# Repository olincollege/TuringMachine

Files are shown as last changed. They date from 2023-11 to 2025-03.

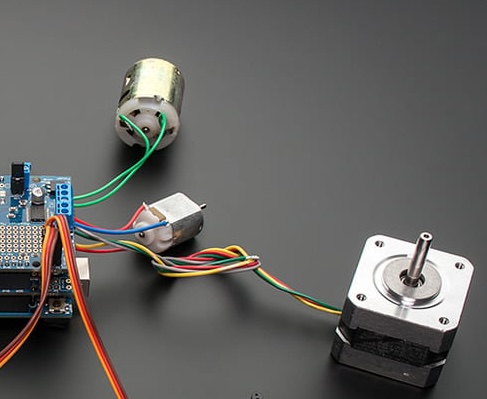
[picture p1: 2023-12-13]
website/turing-machine/images/actuation_motors.jpg

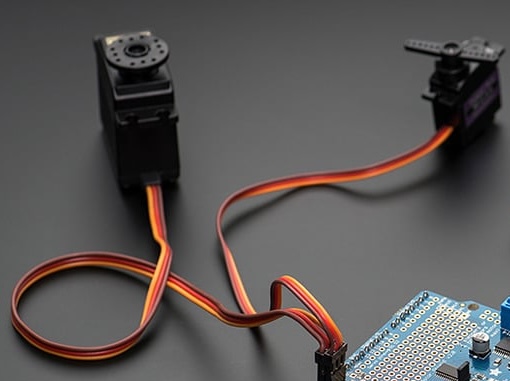
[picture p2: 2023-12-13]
website/turing-machine/images/servos.jpg

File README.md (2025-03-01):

# Turing Machine

**Developed by:** Sparsh Gupta, Mark Belanger, Noah Rand, Joe Leedy, Will Young

Developed at Olin College of Engineering for the Principles of Integrated Engineering (Fall 2023) final project.

[STORY: Olin Students Create Rare, Fully Functional Electromechanical Turing Machine](https://www.olin.edu/articles/story-olin-students-create-rare-fully-functional-electromechanical-turing-machine)

### About
This project is a physical electromechanical implementation of a [Universal Turing Machine](https://en.wikipedia.org/wiki/Universal_Turing_machine) that currently supports basic Turing-computational operations and a few Turing-complete languages.

It could be modified easily to support more Turing-computable operations and Turing-complete languages.

Learn more at: https://olincollege.github.io/pie-2023-03/turing-machine/

### Operations
List of operations currently supported:

- **anbn** (check whether a string has an equal number of 0s and 1s)
- **palindrome** (check whether a string of 0s and 1s is a palindrome)
- **booleanNot** (check whether a string is the boolean NOT/complement of another string)
- **booleanOr** (check whether a string is the boolean OR output of two other strings)
- **addition** (check whether a string is the binary addition output of two other strings)

### Strings/Language

Sample string input formats or languages accepted by the Turing Machine for operations:

**anbn**: 00, 1010, 0110, etc. (any string of even length that consists of 0s and 1s)

**palindrome**: 010, 1001, 111, etc. (any string that consists of 0s and 1s)

**booleanNot**: #0#1, #110#001, #10#01, etc. (two strings u and v that consist of 0s and 1s in the form #u#v 
such that (NOT u = v))

**booleanOr**: #0#1#1, "#101#010#111", etc. (three strings u, v, and w that consist of 0s and 1s in the form #u#v#w 
such that (u OR v = w))

**addition**: #0#1#1, #01#01#10, #101#010#111, etc. (three strings u, v, and w that consist of 0s and 1s in the form #u#v#w 
such that (u + v = w))

### Brief structure of repo

The `CAD` directory houses all the design, fabrication, and mechanical aspects of the project.

The `code` directory contains the entire codebase for simulating the Turing Machine. The subdirectory `main` contains the code flashed to Arduino UNO for motor functions,
state transition, and state transition operations. The subdirectory `symbol_recognition` contains the code for classifying the bits written on tape and is flashed to the ESP32-Cam.

The `website` directory contains the entire code for our hosted website.

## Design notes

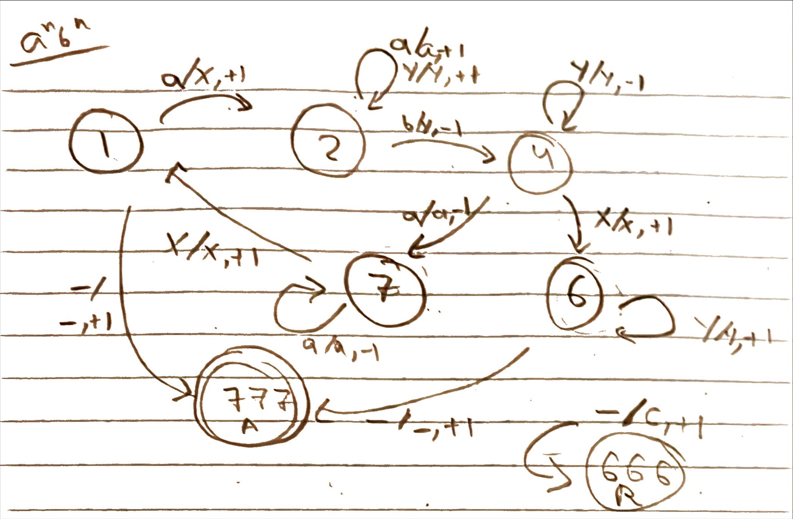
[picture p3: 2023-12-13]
website/turing-machine/images/statetransition.jpeg

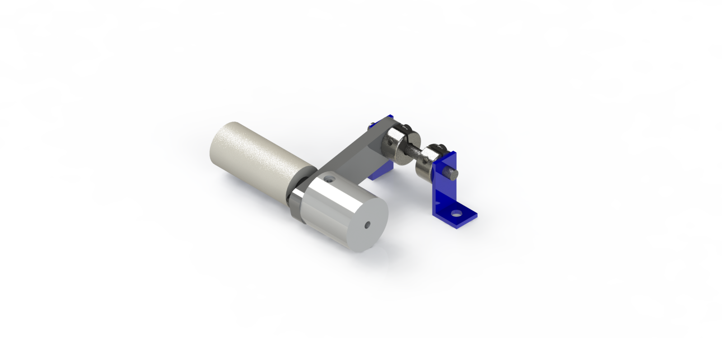
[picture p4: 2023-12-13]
website/turing-machine/images/erasehead_render.png

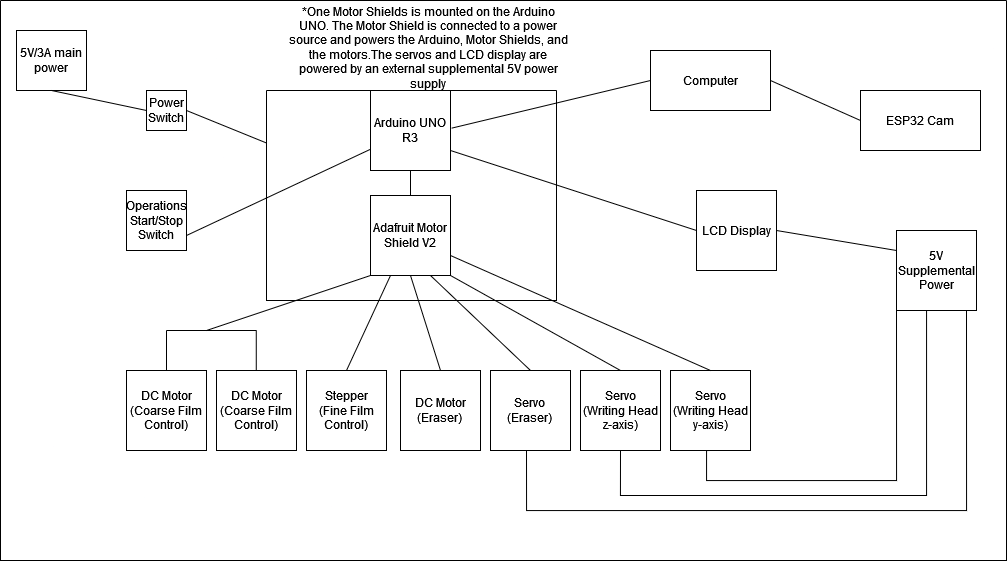
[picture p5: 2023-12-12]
docs/Electrical_Block_Diagram.png

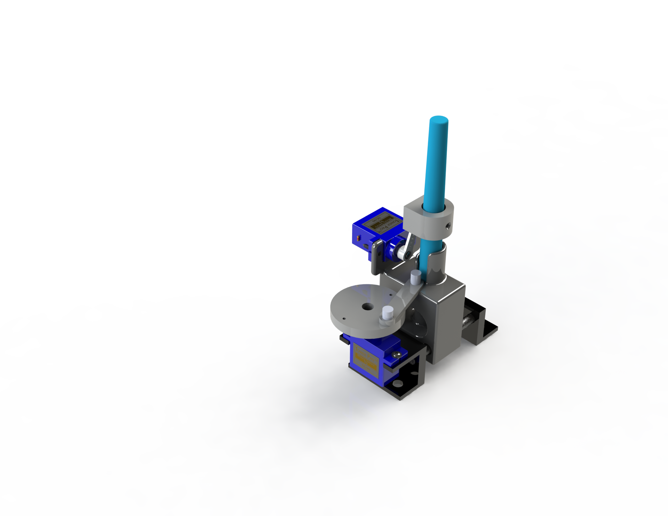
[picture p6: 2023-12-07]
docs/renders/write_head_render.png

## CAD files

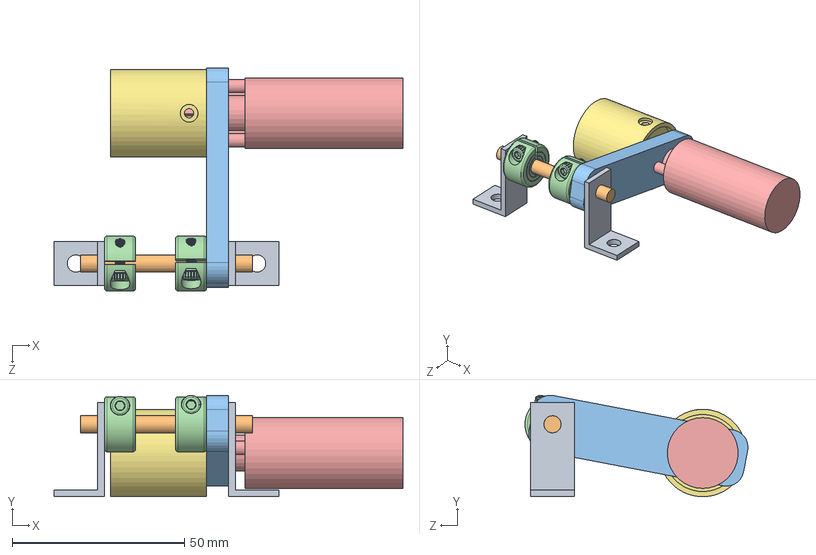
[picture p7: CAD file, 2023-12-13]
CAD/MK3/Erase/eraser_assembly_mk3.SLDASM
101.4 x 29.5 x 64.8 mm
rod_holder x 2
5mm_rod
eraser_swivel
9506T2_Clamping Shaft Collar x 2
eraser_motor
94500A223_316 Stainless Steel Button Head Hex Drive Screws x 2
eraser_wheel

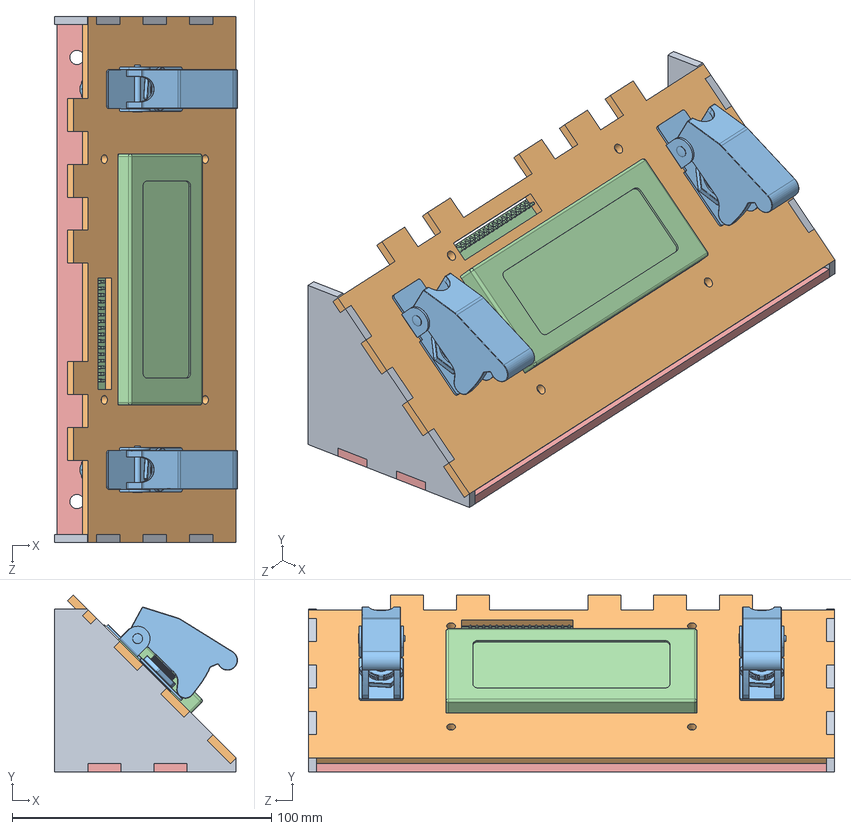
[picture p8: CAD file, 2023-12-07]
CAD/MK3/LCD Mount/lcd_mount_assembly.SLDASM
70.7 x 68.3 x 203.2 mm
lcd_mount_side x 2
lcd_plate
Rocker Safety Switch.step x 2
lcd 2004 i2c v1.step
lcd_mount_bottom

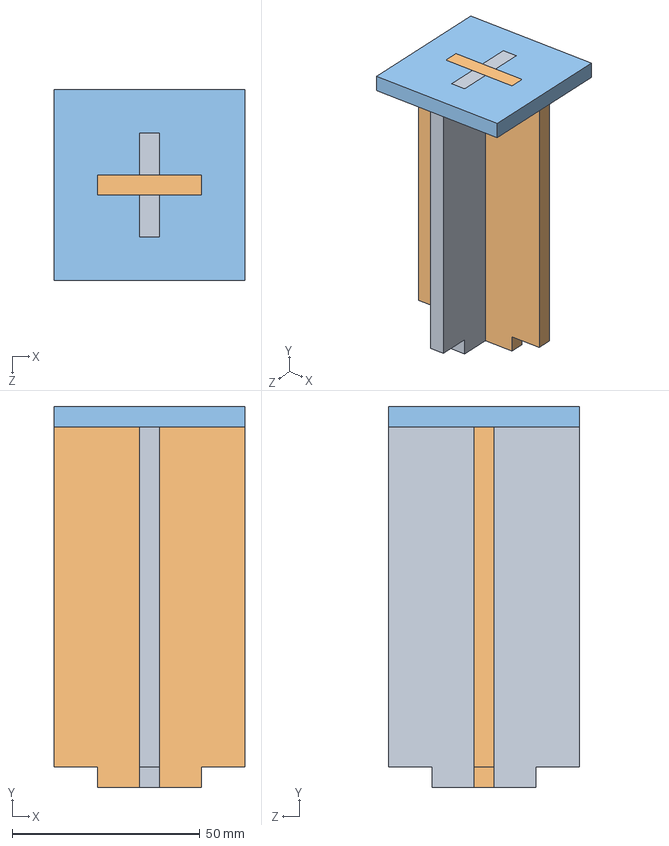
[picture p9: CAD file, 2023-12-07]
CAD/MK3/Tape Runner/tape_runner.SLDASM
50.8 x 101.6 x 50.8 mm
female_slot_runner
male_slot_runner
top_runner

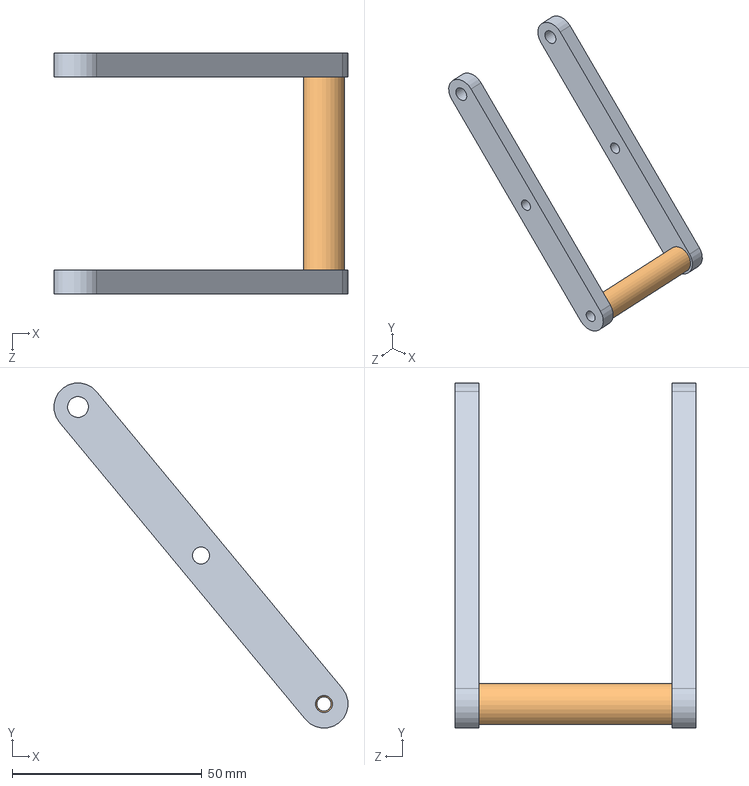
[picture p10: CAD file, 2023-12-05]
CAD/MK3/Tape Tension/Tape_tesnion.SLDASM
77.4 x 90.9 x 63.5 mm
Arm x 2
Roller

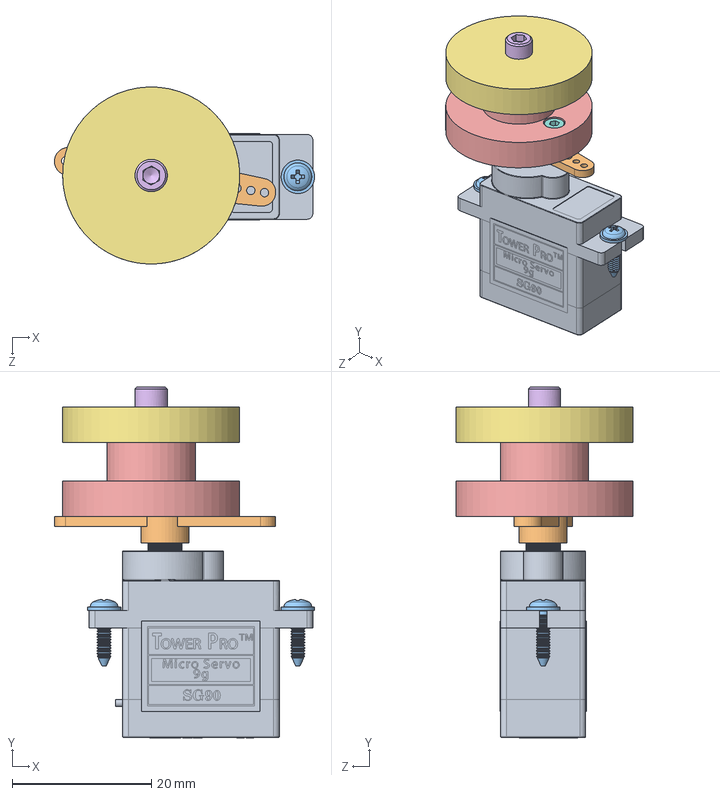
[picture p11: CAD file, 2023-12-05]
CAD/MK3/Erase/servo_assem.SLDASM
37.3 x 50.3 x 25.4 mm
SG90 - Micro Servo 9g - Tower Pro.1
SG90 - Micro Servo 9g - Tower Pro.3
SG90 - Micro Servo 9g - Tower Pro.5 x 2
SG90 - Micro Servo 9g - Tower Pro.6
cam_for_pin
socket head cap screw_ai
cam_part2
socket head cap screw_am x 2

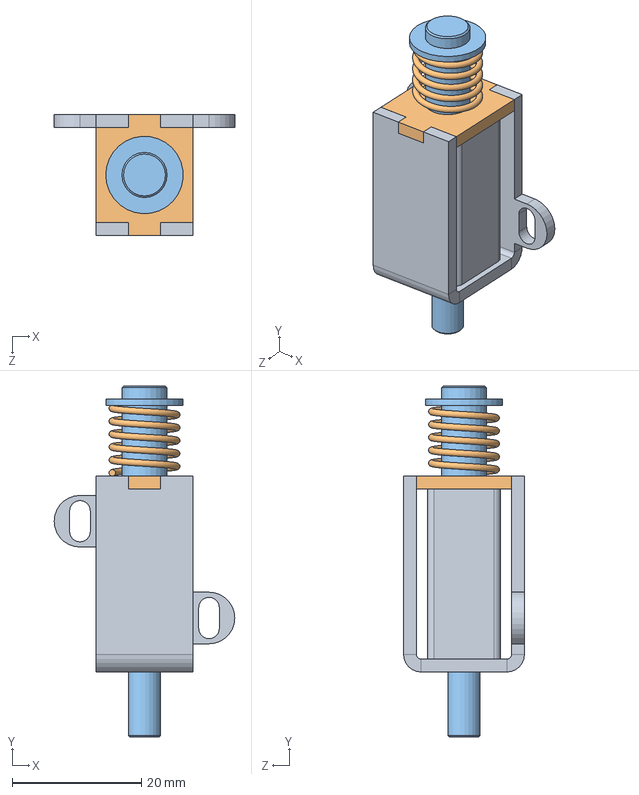
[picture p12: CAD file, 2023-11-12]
CAD/MK3/Erase/solinoid assem.SLDASM
28.0 x 54.4 x 18.8 mm
case
head
bar

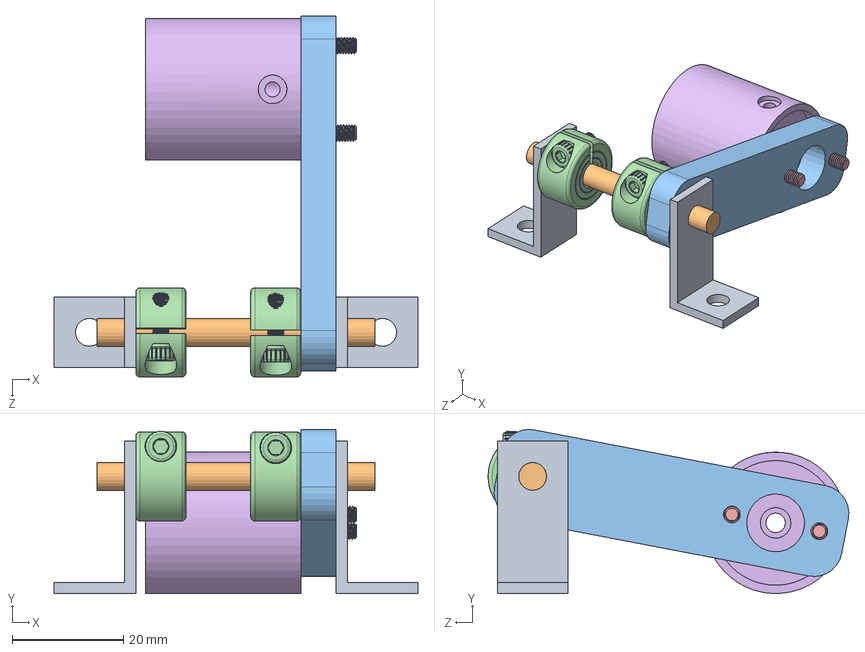
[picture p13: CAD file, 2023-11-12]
CAD/MK3/Erase/eraser_assembly_mk2.SLDASM
65.4 x 29.5 x 64.8 mm
rod_holder x 2
5mm_rod
eraser_swivel
9506T2_Clamping Shaft Collar x 2
94500A223_316 Stainless Steel Button Head Hex Drive Screws x 2
eraser_wheel

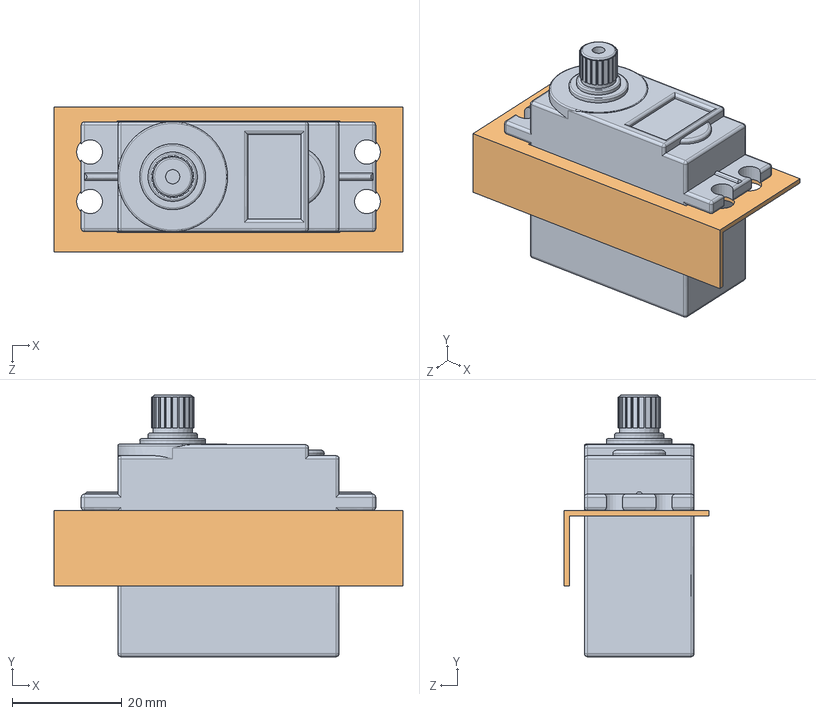
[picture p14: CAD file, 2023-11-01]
CAD/MK3/Erase/eraser_assembly.SLDASM
63.5 x 47.6 x 26.4 mm
Servo MG996R
base_mount_mk1

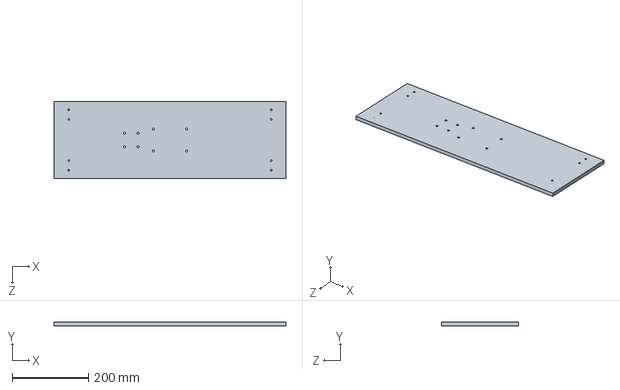
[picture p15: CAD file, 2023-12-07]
CAD/MK3/Base Plate/plate.SLDPRT
609.6 x 9.53 x 203.2 mm

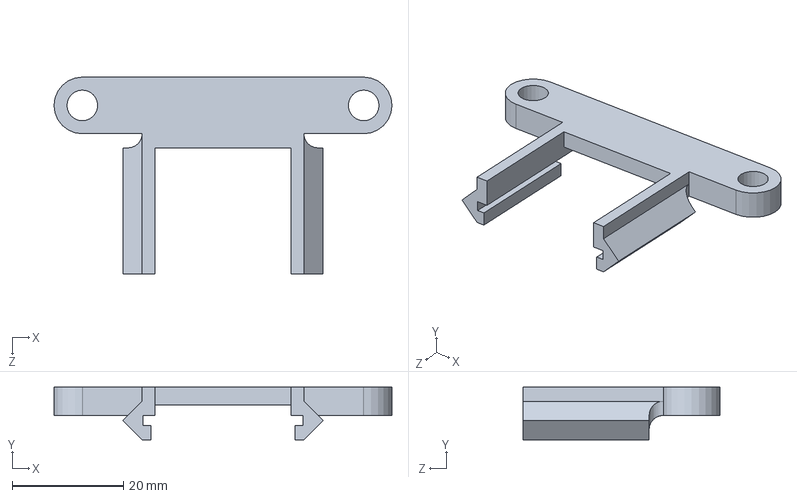
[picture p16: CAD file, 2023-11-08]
CAD/MK3/Camera mount mk2/camera_motherboard_mount.SLDPRT
60.6 x 9.46 x 35.3 mm

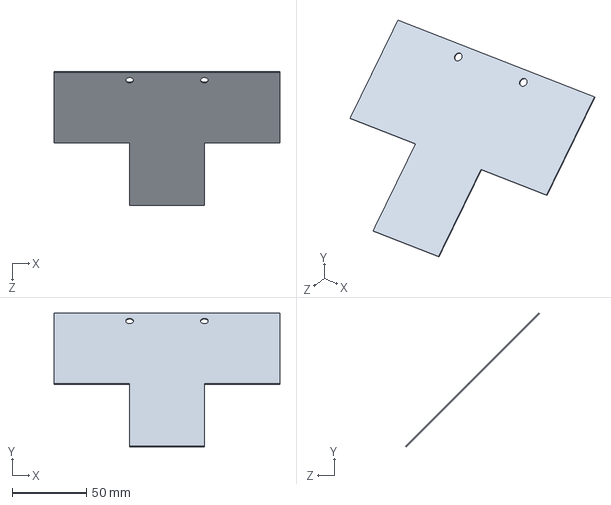
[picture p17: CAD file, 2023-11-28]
CAD/MK3/Camera Shroud/shroud.SLDPRT
152.4 x 90.3 x 90.3 mm

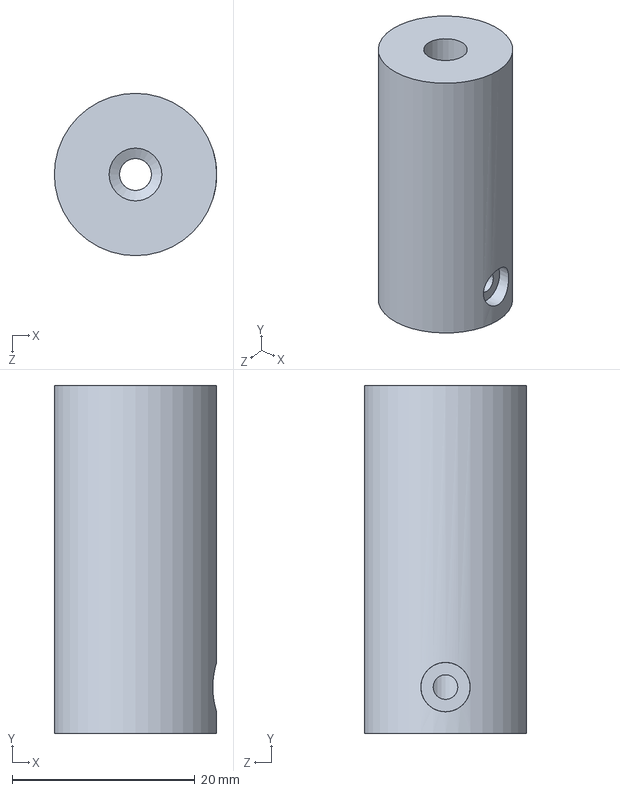
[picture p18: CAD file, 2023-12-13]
CAD/MK3/Erase/eraser_wheel.SLDPRT
17.8 x 38.1 x 17.8 mm

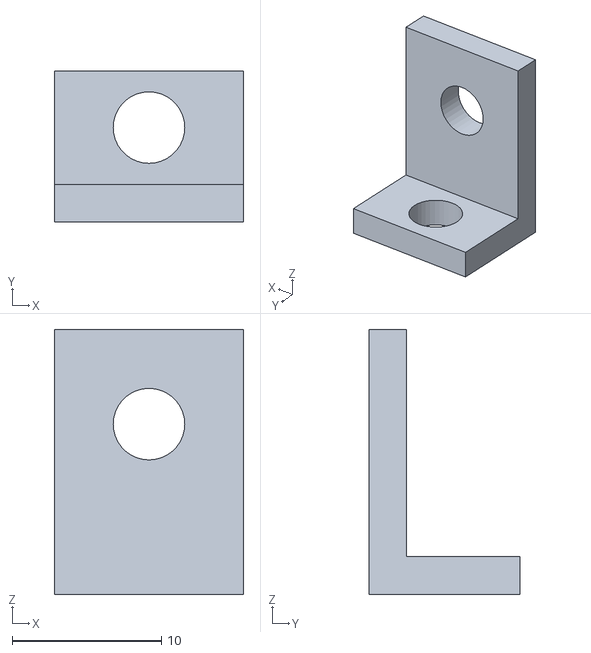
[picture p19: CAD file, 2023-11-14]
CAD/MK3/Fabrication/Baseplate/wheel_hinge_1x_3dp.STL
12.7 x 10.2 x 17.8

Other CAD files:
CAD/MK3/Write/write_rev_3.SLDASM
CAD/MK3/Write/SG90 - Micro Servo 9g - Tower Pro.SLDASM
CAD/MK3/Write/x_write_rev2.SLDASM
CAD/MK3/Write/x_write_rev2_saved.SLDASM
CAD/MK3/Fabrication/Camera Mount/camera_mount_mk2_3dp.STL
CAD/MK1/Camera Mount/Non-adjustable Design/camera_mount_mk1.SLDPRT
CAD/MK1/Camera Mount/Non-adjustable Design/standoff_2.5.SLDPRT
CAD/MK1/Fabrication/Film Sprocket/film_drive_pulley_middle_mk1.STL
CAD/MK1/Fabrication/Film Sprocket/film_drive_pulley_sprocket_part_mk1.STL
CAD/MK1/Fabrication/spool fabrication/spool_keyedshaft.STL
CAD/MK1/Fabrication/spool_sides_v2.DXF
CAD/MK1/Fabrication/spool_sides_v2_part2.DXF
CAD/MK1/Fabrication/spool_v2_part1.STL
CAD/MK1/Fabrication/spool_v2_part2_v2.STL
CAD/MK1/Fabrication/spool_v2_part3.STL
CAD/MK1/Fabrication/spool_v2_part4.STL
CAD/MK1/Fabrication/wheelmount_support.DXF
CAD/MK1/Table/base.SLDASM
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

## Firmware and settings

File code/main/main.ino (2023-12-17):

/*
=================================================================================================================

Main script for the Turing Machine

Learn more at: https://olincollege.github.io/pie-2023-03/turing-machine/

Developed by Sparsh Gupta, Mark Belanger, Noah Rand, Will Young, and Joe Leedy
at Olin College of Engineering, 2023.

=================================================================================================================

List of operations currently supported:

- anbn (check whether a string has an equal number of 0s and 1s)
- palindrome (check whether a string of 0s and 1s is a palindrome)
- booleanNot (check whether a string is the boolean NOT/complement of another string)
- booleanOr (check whether a string is the boolean OR output of two other strings)
- addition (check whether a string is the binary addition output of two other strings)

=================================================================================================================

Sample string input formats or languages accepted by the Turing Machine for operations:

- anbn: 00, 1010, 0101, etc. (any string of even length that consists of 0s and 1s)
- palindrome: 010, 1001, 111, etc. (any string that consists of 0s and 1s)
- booleanNot: #0#1, #110#001, #10#01, etc. (two strings u and v that consist of 0s and 1s in the form #u#v
 such that (NOT u = v))
- booleanOr: #0#1#1, #101#010#111, etc. (three strings u, v, and w that consist of 0s and 1s in the form #u#v#w
 such that (u OR v = w))
- addition: #0#1#1, #01#01#10, #101#010#111, etc. (three strings u, v, and w that consist of 0s and 1s in the form #u#v#w
 such that (u + v = w))

================================================================================================================
*/

// Imports
#include "Arduino.h"
#include "TM_Motor_Movement.h"
#include "string.h"
#include "transition_struct_type.h"
#include "LiquidCrystal_I2C.h"
#include "anbn.h"
#include "palindrome.h"
#include "boolean_not.h"
#include "boolean_or.h"
#include "addition.h"

//------------------------------------------------------------------------------//
//------------------------------------------------------------------------------//
// Provide the input operation and input string to perform on the Turing Machine
String operation = "";
String inputString = "";
//------------------------------------------------------------------------------//
//------------------------------------------------------------------------------//



/*==============================================================================*/
// Instantiate TM Class
String bitstring = inputString;
uint8_t film_dc_pin = 3;
uint8_t stepper_pin = 1;
uint8_t eraser_actuation_pin = 6;
uint8_t eraser_control_pin = 4;
uint8_t eraser_actuation_min = 0;
uint8_t eraser_actuation_max = 180;
uint8_t eraser_speed = 255;
uint8_t erase_all_distance = 1000;
uint8_t stepper_total_steps = 200;
uint8_t stepper_move_steps = 4;
uint8_t stepper_speed = 30;
uint8_t dc_film_speed = 180;
uint8_t draw_actuation_servo_pin = 10;
uint8_t draw_control_servo_pin = 9;
uint8_t marker_up_pos = 180;
uint8_t marker_down_pos = 120;
uint8_t head_min_pos = 5;
uint8_t head_max_pos = 75;
uint8_t zero_lines = 2;
uint8_t bit_space = 25;
uint8_t eraser_head_distance = 150;
uint8_t eraser_distance = 130;
uint8_t eraser_to_write_dist = 49;
uint8_t write_to_camera = 125;

TM_Motor_Movement TM(
        bitstring,
        film_dc_pin,
        stepper_pin,
        eraser_actuation_pin,
        eraser_control_pin,
        eraser_actuation_min,
        eraser_actuation_max,
        eraser_speed,
        erase_all_distance,
        stepper_total_steps,
        stepper_move_steps,
        stepper_speed,
        dc_film_speed,
        draw_actuation_servo_pin,
        draw_control_servo_pin,
        marker_up_pos,
        marker_down_pos,
        head_min_pos,
        head_max_pos,
        zero_lines,
        bit_space,
        eraser_head_distance,
        eraser_distance,
        eraser_to_write_dist,
        write_to_camera
);

/*==============================================================================*/
// LCD display
/*==============================================================================*/
// Instantiate LCD
LiquidCrystal_I2C lcd(0x27,20,4);

void displayOnLCD(String line1, String line2, String line3, String line4) {
    lcd.clear();
    lcd.setCursor(0, 0);
    lcd.print(line1);
    lcd.setCursor(0, 1);
    lcd.print(line2);
    lcd.setCursor(0, 3);
    lcd.print(line3);
    lcd.setCursor(10, 3);
    lcd.print(line4);
}


/*==============================================================================*/
// Read Symbol
/*==============================================================================*/
char first_bit, second_bit, third_bit;
String symbol_bits;
char symbol;

char readSymbol() {
    // Read first bit and move one symbol forward
    delay(5000);
    first_bit = Serial.read();
    TM.moveOneBitForward();

    // Read second bit and move one symbol forward
    delay(5000);
    second_bit = Serial.read();
    TM.moveOneBitForward();

    // Read third bit and move one symbol forward
    delay(5000);
    third_bit = Serial.read();

    // create symbol bitstring
    symbol_bits = first_bit + second_bit + third_bit;

    // Map to symbol
    if (strcmp(symbol_bits.c_str(), "000") == 0) {
        symbol = '#';
    } else if (strcmp(symbol_bits.c_str(), "010") == 0) {
        symbol = '0';
    } else if (strcmp(symbol_bits.c_str(), "011") == 0) {
        symbol = '1';
    } else if (strcmp(symbol_bits.c_str(), "101") == 0) {
        symbol = 'X';
    } else if (strcmp(symbol_bits.c_str(), "110") == 0) {
        symbol = 'Y';
    } else if (strcmp(symbol_bits.c_str(), "111") == 0) {
        symbol = '_';
    } else {
        symbol = 'E';
    }

    return symbol;

    lcd.setCursor(0,3);     
    lcd.print("Symbol: " + symbol);
}

/*==============================================================================*/
// State Transition
/*==============================================================================*/

// Function to choose which draw function to use for symbol
void drawSymbol(char symbol_to_draw) {
    if (symbol_to_draw == 'X') {
        TM.drawX();
    } else if (symbol_to_draw == 'Y') {
        TM.drawY();
    } else if (symbol_to_draw == '_') {
        TM.drawBlank();
    }
}

// ---------------------
// anbn state transition
// ---------------------
char stateTransition_anbn() {

    // Defining input and output
    TM_transition_input anbn_input;
    TM_transition_output anbn_output;

    // Initialize start state and read initial symbol
    anbn_input.state = 1;
    anbn_input.symbol = readSymbol();

    lcd.setCursor(0,0);
    lcd.print("Operation: " + operation); 
    lcd.setCursor(0,1);     
     
    lcd.setCursor(0,3);     
    lcd.print("State: " + anbn_input.state);  
    lcd.setCursor(10,3);     
    lcd.print("Symbol: " + anbn_input.symbol); 

    while (anbn_input.state < 100) {
        // Obtain one transition output
        anbn_output = anbn(anbn_input);

        // Halting state: Accept or Reject
        if (anbn_output.state == 77) {
            return 'A';
        } else if (anbn_output.state == 66) {
            return 'R';
        }

        // Write new symbol or skip drawing if same symbol
        if (anbn_input.symbol != anbn_output.symbol) {

            // Erase input symbol first
            TM.eraseOneSymbol();

            // Draw output symbol
            drawSymbol(anbn_output.symbol);

            // Move pointer based on output
            if (anbn_output.move_pointer == 1) {
                TM.moveOneSymbolForward();
            } else {
                TM.moveOneSymbolBackward();
            }
        }
        else {
            // Just move pointer based on output
            if (anbn_output.move_pointer == 1) {
                TM.moveOneSymbolForward();
            } else {
                TM.moveOneSymbolBackward();
            }
        }

        // Next state and symbol
        anbn_input.state = anbn_output.state;
        anbn_input.symbol = readSymbol();

        
    }
}

// ---------------------------
// palindrome state transition
// ---------------------------
char stateTransition_palindrome() {

    // Defining input and output
    TM_transition_input palindrome_input;
    TM_transition_output palindrome_output;

    // Initialize start state and read initial symbol
    palindrome_input.state = 1;
    palindrome_input.symbol = readSymbol();

    displayOnLCD("Turing Machine",
                 "Operation: " + operation,
                 "State: " + palindrome_input.state,
                 "Symbol: " + palindrome_input.symbol);

    while (palindrome_input.state < 100) {
        // Obtain one transition output
        palindrome_output = palindrome(palindrome_input);

        // Halting state: Accept or Reject
        if (palindrome_output.state == 77) {
            return 'A';
        } else if (palindrome_output.state == 66) {
            return 'R';
        }

        // Write new symbol or skip drawing if same symbol
        if (palindrome_input.symbol != palindrome_output.symbol) {

            // Erase input symbol first
            TM.eraseOneSymbol();

            // Draw output symbol
            drawSymbol(palindrome_output.symbol);

            // Move pointer based on output
            if (palindrome_output.move_pointer == 1) {
                TM.moveOneSymbolForward();
            } else {
                TM.moveOneSymbolBackward();
            }
        }
        else {
            // Just move pointer based on output
            if (palindrome_output.move_pointer == 1) {
                TM.moveOneSymbolForward();
            } else {
                TM.moveOneSymbolBackward();
            }
        }

        // Next state and symbol
        palindrome_input.state = palindrome_output.state;
        palindrome_input.symbol = readSymbol();

        displayOnLCD("Turing Machine",
                     "Operation: " + operation,
                     "State: " + palindrome_input.state,
                     "Symbol: " + palindrome_input.symbol);
    }
}

// ---------------------------
// booleanNot state transition
// ---------------------------
char stateTransition_booleanNot() {

    // Defining input and output
    TM_transition_input booleanNot_input;
    TM_transition_output booleanNot_output;

    // Initialize start state and read initial symbol
    booleanNot_input.state = 1;
    booleanNot_input.symbol = readSymbol();

    displayOnLCD("Turing Machine",
                 "Operation: " + operation,
                 "State: " + booleanNot_input.state,
                 "Symbol: " + booleanNot_input.symbol);

    while (booleanNot_input.state < 100) {
        // Obtain one transition output
        booleanNot_output = booleanNot(booleanNot_input);

        // Halting state: Accept or Reject
        if (booleanNot_output.state == 77) {
            return 'A';
        } else if (booleanNot_output.state == 66) {
            return 'R';
        }

        // Write new symbol or skip drawing if same symbol
        if (booleanNot_input.symbol != booleanNot_output.symbol) {

            // Erase input symbol first
            TM.eraseOneSymbol();

            // Draw output symbol
            drawSymbol(booleanNot_output.symbol);

            // Move pointer based on output
            if (booleanNot_output.move_pointer == 1) {
                TM.moveOneSymbolForward();
            } else {
                TM.moveOneSymbolBackward();
            }
        }
        else {
            // Just move pointer based on output
            if (booleanNot_output.move_pointer == 1) {
                TM.moveOneSymbolForward();
            } else {
                TM.moveOneSymbolBackward();
            }
        }

        // Next state and symbol
        booleanNot_input.state = booleanNot_output.state;
        booleanNot_input.symbol = readSymbol();

        displayOnLCD("Turing Machine",
                     "Operation: " + operation,
                     "State: " + booleanNot_input.state,
                     "Symbol: " + booleanNot_input.symbol);
    }
}


// ---------------------------
// booleanOr state transition
// ---------------------------
char stateTransition_booleanOr() {

    // Defining input and output
    TM_transition_input booleanOr_input;
    TM_transition_output booleanOr_output;

    // Initialize start state and read initial symbol
    booleanOr_input.state = 1;
    booleanOr_input.symbol = readSymbol();

    displayOnLCD("Turing Machine",
                 "Operation: " + operation,
                 "State: " + booleanOr_input.state,
                 "Symbol: " + booleanOr_input.symbol);

    while (booleanOr_input.state < 100) {
        // Obtain one transition output
        booleanOr_output = booleanOr(booleanOr_input);

        // Halting state: Accept or Reject
        if (booleanOr_output.state == 77) {
            return 'A';
        } else if (booleanOr_output.state == 66) {
            return 'R';
        }

        // Write new symbol or skip drawing if same symbol
        if (booleanOr_input.symbol != booleanOr_output.symbol) {

            // Erase input symbol first
            TM.eraseOneSymbol();

            // Draw output symbol
            drawSymbol(booleanOr_output.symbol);

            // Move pointer based on output
            if (booleanOr_output.move_pointer == 1) {
                TM.moveOneSymbolForward();
            } else {
                TM.moveOneSymbolBackward();
            }
        }
        else {
            // Just move pointer based on output
            if (booleanOr_output.move_pointer == 1) {
                TM.moveOneSymbolForward();
            } else {
                TM.moveOneSymbolBackward();
            }
        }

        // Next state and symbol
        booleanOr_input.state = booleanOr_output.state;
        booleanOr_input.symbol = readSymbol();

        displayOnLCD("Turing Machine",
                     "Operation: " + operation,
                     "State: " + booleanOr_input.state,
                     "Symbol: " + booleanOr_input.symbol);
    }
}


// -------------------------
// addition state transition
// -------------------------
char stateTransition_addition() {

    // Defining input and output
    TM_transition_input addition_input;
    TM_transition_output addition_output;

    // Initialize start state and read initial symbol
    addition_input.state = 1;
    addition_input.symbol = readSymbol();

    lcd.setCursor(0,0);
    lcd.print("Operation: " + operation);
    lcd.setCursor(0,1);

    lcd.setCursor(0,3);
    lcd.print("State: " + addition_input.state);
    lcd.setCursor(10,3);
    lcd.print("Symbol: " + addition_input.symbol);

    while (addition_input.state < 100) {
        // Obtain one transition output
        addition_output = addition(addition_input);

        // Halting state: Accept or Reject
        if (addition_output.state == 77) {
            return 'A';
        } else if (addition_output.state == 66) {
            return 'R';
        }

        // Write new symbol or skip drawing if same symbol
        if (addition_input.symbol != addition_output.symbol) {

            // Erase input symbol first
            TM.eraseOneSymbol();

            // Draw output symbol
            drawSymbol(addition_output.symbol);

            // Move pointer based on output
            if (addition_output.move_pointer == 1) {
                TM.moveOneSymbolForward();
            } else {
                TM.moveOneSymbolBackward();
            }
        }
        else {
            // Just move pointer based on output
            if (addition_output.move_pointer == 1) {
                TM.moveOneSymbolForward();
            } else {
                TM.moveOneSymbolBackward();
            }
        }

        // Next state and symbol
        addition_input.state = addition_output.state;
        addition_input.symbol = readSymbol();


    }
}



// ---------------------------------------------------------------
// Operation state transition
// ---------------------------------------------------------------
char stateTransitionResult; // To return the result of computation
// Select stateTransition TM based on operation
char stateTransition(const String& operation) {
    if (operation == "anbn") {
        stateTransitionResult = stateTransition_anbn();
        return stateTransitionResult;
    }
    else if (operation == "palindrome") {
        stateTransitionResult = stateTransition_palindrome();
        return stateTransitionResult;
    }
    else if (operation == "booleanNot") {
        stateTransitionResult = stateTransition_booleanNot();
        return stateTransitionResult;
    }
    else if (operation == "booleanOr") {
        stateTransitionResult = stateTransition_booleanOr();
        return stateTransitionResult;
    }
    else if (operation == "addition") {
        stateTransitionResult = stateTransition_addition();
        return stateTransitionResult;
    }
    else {
        return 'Error';
    }
}


/*==============================================================================*/
// Arduino
/*==============================================================================*/



// To store the output of TM computation
char result;

// Arduino
void setup() {
    // State transition Switch
    pinMode(2, INPUT_PULLUP);
    pinMode(13, OUTPUT);

    int sensorVal = digitalRead(2);

    // LCD
    lcd.init(); 
    lcd.backlight(); 
    lcd.setCursor(0,0);
    lcd.print("Turing Machine"); 
    lcd.setCursor(0,1); 
    lcd.print("Op: " + operation); 
    lcd.setCursor(0,2);    
    lcd.print("String: " + inputString);   
    lcd.setCursor(0,3);      
    lcd.print("Computing...");


    if (sensorVal == HIGH) {
      // Setup motor functions
      TM.begin();

      // Draw the inputString
      TM.drawAll();

      // Move start of string (first symbol) under camera
      TM.goToCamera();

      // Obtain computation result using State Transition
      result = stateTransition(operation);

      // Display final result on LCD
      String resultMessage;
      if (result == 'A') {
          resultMessage = "Accept";
      } else if (result == 'R') {
          resultMessage = "Reject";
      } else {
          resultMessage = "Error!";
      }

      lcd.clear();
      lcd.setCursor(0,0);
      lcd.print("Turing Machine"); 
      lcd.setCursor(0,1); 
      lcd.print("Op: " + operation); 
      lcd.setCursor(0,2);    
      lcd.print("String: " + inputString);   
      lcd.setCursor(0,3);      
      lcd.print("Result:" + resultMessage);

      // Erase string on tape
      TM.eraseAll();
    }
}

void loop() {
 // Nothing needed
}

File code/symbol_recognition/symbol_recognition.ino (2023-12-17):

#include "esp_camera.h"

#define PWDN_GPIO_NUM     32
#define RESET_GPIO_NUM    -1
#define XCLK_GPIO_NUM      0
#define SIOD_GPIO_NUM     26
#define SIOC_GPIO_NUM     27

#define Y9_GPIO_NUM       35
#define Y8_GPIO_NUM       34
#define Y7_GPIO_NUM       39
#define Y6_GPIO_NUM       36
#define Y5_GPIO_NUM       21
#define Y4_GPIO_NUM       19
#define Y3_GPIO_NUM       18
#define Y2_GPIO_NUM        5
#define VSYNC_GPIO_NUM    25
#define HREF_GPIO_NUM     23
#define PCLK_GPIO_NUM     22

// LED Illuminator
#define CONFIG_LED_ILLUMINATOR_ENABLED
#define CONFIG_LED_LEDC_PIN 4
#define CONFIG_LED_MAX_INTENSITY 255
#define CONFIG_LED_LEDC_TIMER LEDC_TIMER_0
#define CONFIG_LED_LEDC_CHANNEL LEDC_CHANNEL_0

const int pwmfreq = 50000;     // 50K pwm frequency
const int pwmresolution = 9;   // duty cycle bit range

#define FRAME_SIZE FRAMESIZE_QQVGA
#define WIDTH 160
#define HEIGHT 120
#define THRESHOLD 127

float features[HEIGHT*WIDTH] = { 0 };

void setup() {
  Serial.begin(115200);
  delay(1000); // Allow time for serial monitor to open

  // Configure LED PWM channel
  //ledcSetup(CONFIG_LED_LEDC_CHANNEL, pwmfreq, pwmresolution);
  //ledcAttachPin(CONFIG_LED_LEDC_PIN, CONFIG_LED_LEDC_CHANNEL);
  
  // Set LED brightness
  //ledcWrite(CONFIG_LED_LEDC_CHANNEL, 150);
  
  Serial.println(setup_camera(FRAME_SIZE) ? "Camera Initialized" : "Camera Initialization Failed");
  delay(2000); // Allow time for the camera to stabilize before attempting capture
}
void loop() {
  if (!capture_still()) {
    Serial.println("Failed to capture");
    delay(2000);
    return;
  }
  delay(3000);
}

bool setup_camera(framesize_t frameSize) {
    camera_config_t config;

    config.ledc_channel = LEDC_CHANNEL_0;
    config.ledc_timer = LEDC_TIMER_0;
    config.pin_d0 = Y2_GPIO_NUM;
    config.pin_d1 = Y3_GPIO_NUM;
    config.pin_d2 = Y4_GPIO_NUM;
    config.pin_d3 = Y5_GPIO_NUM;
    config.pin_d4 = Y6_GPIO_NUM;
    config.pin_d5 = Y7_GPIO_NUM;
    config.pin_d6 = Y8_GPIO_NUM;
    config.pin_d7 = Y9_GPIO_NUM;
    config.pin_xclk = XCLK_GPIO_NUM;
    config.pin_pclk = PCLK_GPIO_NUM;
    config.pin_vsync = VSYNC_GPIO_NUM;
    config.pin_href = HREF_GPIO_NUM;
    config.pin_sccb_sda = SIOD_GPIO_NUM;
    config.pin_sccb_scl = SIOC_GPIO_NUM;
    config.pin_pwdn = PWDN_GPIO_NUM;
    config.pin_reset = RESET_GPIO_NUM;
    config.xclk_freq_hz = 20000000;
    config.pixel_format = PIXFORMAT_GRAYSCALE;
    config.frame_size = frameSize;
    config.jpeg_quality = 12;
    config.fb_count = 1;

    bool ok = esp_camera_init(&config) == ESP_OK;

    sensor_t *sensor = esp_camera_sensor_get();

    sensor->set_framesize(sensor, frameSize);
    sensor->set_brightness(sensor, 2);
    sensor->set_contrast(sensor, 2);
    sensor->set_awb_gain(sensor, 1);
    sensor->set_wb_mode(sensor, 0);

    return ok;
}
bool capture_still() {
  camera_fb_t *frame = esp_camera_fb_get();

  if (!frame) {
    Serial.println("Failed to capture image");
    return false;
  }

  // Reset all the features
  for (size_t i = 0; i < HEIGHT * WIDTH; i++)
    features[i] = 0;

  // For each pixel, compute the position in the downsampled image
  for (size_t i = 0; i < frame->len; i++) {
    const uint16_t x = i % WIDTH;
    const uint16_t y = i / WIDTH;
    const uint16_t j = y * WIDTH + x;

    // Compute features by averaging pixel values
    features[j] += frame->buf[i];
  }

  int total_features = 0;
  //Apply threshold after computing features
  for (size_t i = 0; i < HEIGHT * WIDTH; i++) {
    features[i] = (features[i] > THRESHOLD) ? 0 : 1;

    total_features += features[i];
  }

  //Serial.println(total_features);

  // Classify symbols using conditionals
  if (total_features < 4000) {
    Serial.println("1");
  }
  else {
    Serial.println("0");
  }

  esp_camera_fb_return(frame); // Free frame buffer memory after processing

  return true;
}

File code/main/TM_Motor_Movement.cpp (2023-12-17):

#include "Arduino.h"
#include <Adafruit_MotorShield.h>
#include "TM_Motor_Movement.h"
#include <Servo.h>
#include "string.h"

TM_Motor_Movement::TM_Motor_Movement(
        String  bitstring,                  // Starting input bitstring
        uint8_t film_dc_pin,                // Pin that the tape actuation DC motors are conencted to on the Motor Shield
        uint8_t stepper_pin,                // Pin that the tape actuation stepper motor is connected to on the Motor Shield
        uint8_t eraser_actuation_pin,       // Pin that the eraser head actuation servo is connected to on the Arduino
        uint8_t eraser_control_pin,         // Pin that the eraser head DC motor is connected to on the Motor Sheild
        uint8_t eraser_actuation_min,       // Low / eraser down position for the eraser head servo
        uint8_t eraser_actuation_max,       // High / eraser up position for the eraser head servo
        uint8_t erase_all_distance,         // Total stepper steps to eraser large sections on the tape after use
        uint8_t eraser_speed,               // 8 bit speed of the eraser DC motor
        uint8_t stepper_total_steps,        // The total number of steps that the stepper motor has
        uint8_t stepper_move_steps,         // Total number of steps for the stepper to move at once
        uint8_t stepper_speed,              // 8 bit speed for the stepper motor (microsteps used)
        uint8_t dc_film_speed,              // 8 bit speed of the tape actuation DC motors
        uint8_t draw_actuation_servo_pin,   // Pin for the servo that controls the vertical motion of the marker
        uint8_t draw_control_servo_pin,     // Pin the for the servo that controls the horizontal motion of the writing head
        uint8_t marker_up_pos,              // Servo positon for the marker in the up position
        uint8_t marker_down_pos,            // Servo position for the marker in the down position
        uint8_t head_min_pos,               // Servo position for the writing head at the start position
        uint8_t head_max_pos,               // Servo position for the writing head at the fully extended position
        uint8_t zero_lines,                 // Number of zig zag lines when drawing zero symbol
        uint8_t bit_space,                  // Stepper spaces between bits
        uint8_t eraser_head_distance,       // Stepper steps from under the camera to under the eraser head
        uint8_t eraser_distance,            // Stepper steps to erase one symbol
        uint8_t eraser_to_write_dist,       // Stepper steps from ther eraser to under the writing head
        uint8_t write_to_camera             // Stepper steps from under the writing head to under the camera
) :

        start_bitstring(bitstring),

        film_dcM_pin(film_dc_pin),
        dcM_film_speed(dc_film_speed),

        stepperM_pin(stepper_pin),
        stepperM_total_steps(stepper_total_steps),
        stepperM_move_steps(stepper_move_steps),
        stepperM_speed(stepper_speed),

        eraser_actuationM_pin(eraser_actuation_pin),
        eraser_controlM_pin(eraser_control_pin),
        eraser_actuationM_min(eraser_actuation_min),
        eraser_actuationM_max(eraser_actuation_max),
        eraserM_speed(eraser_speed),
        eraserM_head_distance(eraser_head_distance),
        eraserM_distance(eraser_distance),
        eraserM_to_write_dist(eraser_to_write_dist),
        erase_all_dist(erase_all_distance),

        draw_actuation_servoM_pin(draw_actuation_servo_pin),
        draw_control_servoM_pin(draw_control_servo_pin),
        marker_down_posi(marker_down_pos),
        marker_up_posi(marker_up_pos),
        head_min(head_min_pos),
        head_max(head_max_pos),
        zero_lines_num(zero_lines),
        bit_spacing(bit_space),
        write_to_cam(write_to_camera)
{

};

void TM_Motor_Movement::begin() {
    //Serial.begin(9600);
    AFMS = Adafruit_MotorShield();
    //Serial.println("MotorShield Found!");
    fineFilmControl = AFMS.getStepper(stepperM_total_steps, stepperM_pin);
    //Serial.println("Stepper Found!");
    coarseFilmControl = AFMS.getMotor(film_dcM_pin);
    //Serial.println("DC Motors Found!");
    eraserControl = AFMS.getMotor(eraser_controlM_pin);
    //Serial.println("Eraser Found!");
    eraserActuation.attach(eraser_actuationM_pin);
    eraserActuation.write(eraser_actuationM_min);
    delay(300);
    //Serial.println("Eraser acuation home!");
    drawingActuation.attach(draw_actuation_servoM_pin);
    drawingActuation.write(marker_up_posi);
    delay(300);
    //Serial.println("Drawing acuation home!");
    drawingControl.attach(draw_control_servoM_pin);
    drawingControl.write(head_min);
    delay(300);
    //Serial.println("Drawing control home!");
    AFMS.begin();
    //Serial.println("Initiation Successful!");
}

void TM_Motor_Movement::moveFilmForward() {
    // Method to move the film forward by a small increment for drawing symbols

    fineFilmControl->setSpeed(stepperM_speed);
    coarseFilmControl->setSpeed(dcM_film_speed);
    coarseFilmControl->run(FORWARD);
    fineFilmControl->step(stepperM_move_steps, FORWARD, MICROSTEP);
    coarseFilmControl->setSpeed(0);
    delay(500);
    // Serial.println("Film Forward!");
}

void TM_Motor_Movement::moveFilmBackward() {
    // Method to move the film forward by a small increment for drawing symbols

    fineFilmControl->setSpeed(stepperM_speed);
    coarseFilmControl->setSpeed(dcM_film_speed);
    coarseFilmControl->run(BACKWARD);
    fineFilmControl->step(stepperM_move_steps, BACKWARD, MICROSTEP);
    coarseFilmControl->setSpeed(0);
    delay(500);
    // Serial.println("Film Backward!");
}

void TM_Motor_Movement::moveOneBitForward() {
    // Methed to advance the film a forward by a defined spacing for each bit

    fineFilmControl->setSpeed(stepperM_speed);
    coarseFilmControl->setSpeed(dcM_film_speed);
    coarseFilmControl->run(FORWARD);
    fineFilmControl->step(bit_spacing, FORWARD, MICROSTEP);
    coarseFilmControl->setSpeed(0);
    delay(500);
}

void TM_Motor_Movement::moveOneSymbolForward() {
    // Method to advance the film forward by one symbol

    moveOneBitForward();
    delay(50);
    moveOneBitForward();
    delay(50);
    moveOneBitForward();
    delay(50);
}

void TM_Motor_Movement::moveOneBitBackward() {
    // Methed to advance the film a backward by a defined spacing for each bit

    fineFilmControl->setSpeed(stepperM_speed);
    coarseFilmControl->setSpeed(dcM_film_speed);
    coarseFilmControl->run(BACKWARD);
    fineFilmControl->step(bit_spacing, BACKWARD, MICROSTEP);
    coarseFilmControl->setSpeed(0);
    delay(500);
}

void TM_Motor_Movement::moveOneSymbolBackward() {
    // Method to advance the film forward by one symbol

    moveOneBitBackward();
    delay(50);
    moveOneBitBackward();
    delay(50);
    moveOneBitBackward();
    delay(50);
}
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

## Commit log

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2023-10-26 Table CAD start
    Task list remaining:
    - get film sprocket sizing and tooth positions right
    - Figure out stepper gear ratio
    - way to hold shafts in
    - sprocket spacers (stepper one is further than others
    -
    [3764N107_High-Strength Gt Timing Belt Pulley.SLDPRT, 3764N113_High-Strength Gt Timing Belt Pulley.SLDPRT, 5314A3_Polished Chrome-Plated Combination Wrench.SLDP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]
2023-10-29 Camera mount w/o mounting holes, stl of same
    [camera_mount_mk1_holeless.SLDPRT, camera_mount_mk1_holeless_3dp.STL, read_write_top.SLDPRT]
2023-10-29 added sliding mount and static mount with mounting holes
    Sliding mount is what I think we'll use for sprint one to determine where we want the camera in the y-axis.
    [camera_mount_mk1.SLDPRT, camera_mount_mk1_3dp.STL, camera_mount_mk1_holeless.SLDPRT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]
2023-10-30 gear ratio stuff probobly
    [3764N107_High-Strength Gt Timing Belt Pulley.SLDPRT, 3764N113_High-Strength Gt Timing Belt Pulley.SLDPRT, base.SLDASM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]
2023-10-30 fix spacing for belt irl
    [3764N107_High-Strength Gt Timing Belt Pulley.SLDPRT, 3764N113_High-Strength Gt Timing Belt Pulley.SLDPRT, 92095A214_Button Head Hex Drive Screw.SLDPRT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]
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2023-10-30 Film cog finished hopefully
    [3764N107_High-Strength Gt Timing Belt Pulley.SLDPRT, 3764N113_High-Strength Gt Timing Belt Pulley.SLDPRT, film.SLDPRT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]
2023-10-31 added laser cut files
    [box_faces.SLDPRT, box_faces_bottom.DXF, box_faces_front.DXF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]
2023-10-31 make film sprocket manufacturable
    [film_drive_pulley.SLDPRT]
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2023-11-01 Working Symbol Recognition (but bad classification acc)
    [dataset.csv]
2023-11-01 fix hole sizing, do eraser things start
    [##Servo_MG_996R.SLDPRT, 5mm_rod.SLDPRT, base_mount_mk1.SLDPRT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]
2023-11-01 modified hole spacing on static mount to match sliding mount
    [camera_mount_mk1.SLDPRT, slide_interface_mk1.SLDPRT]
2023-11-01 added standoff and .3mf files for fabrication
    [camera_mount_fixed.SLDASM, camera_mount_mk1.SLDPRT, camera_mount_mk1_3dp.STL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]
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2023-11-02 Why are there so many changes?
    [3764N107_High-Strength Gt Timing Belt Pulley.SLDPRT, 3764N113_High-Strength Gt Timing Belt Pulley.SLDPRT, 92981A778_Alloy Steel Shoulder Screws.SLDPRT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]
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2023-11-03 Add bolt holes to film sprocket
    [film_drive_pulley.SLDPRT]
2023-11-05 Making changes to table cad
    Modified tape cover to reflect new spools and added additional configs for delrin
    [3764N107_High-Strength Gt Timing Belt Pulley.SLDPRT, 3764N113_High-Strength Gt Timing Belt Pulley.SLDPRT, 9271K71_Torsion Spring.SLDPRT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]
2023-11-06 film spool changes
    tooth count and mounting hole sizes
    [film_drive_pulley.SLDPRT, film_drive_pulley_middle_mk1.STL, film_drive_pulley_sprocket_part_mk1.STL]
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2023-11-06 modified camera mount for mk2
    [camera_motherboard_mount.SLDPRT, camera_mount_mk1_3dp.STL, standoff_2.5.SLDPRT]
2023-11-06 add some holes, change write head
    [box_faces.SLDPRT, rod_holder_rev2.SLDPRT, x_write_rev2.SLDASM]
2023-11-07 Created tape runner parts + subassembly
    [Component5(Mirror).step.SLDPRT, Component5.step.SLDPRT, ESP3-CAM v5 - black pcb (1).step.SLDASM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]
2023-11-07 trying to fix commit problems
    [Component5(Mirror).step.SLDPRT, Component5.step.SLDPRT, ESP3-CAM v5 - black pcb (1).step.SLDASM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]
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2023-11-07 added laser cut files for tape runner
    [bottom_runner.DXF, female_slot_runner.DXF, male_slot_runner.DXF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]
2023-11-08 Finalized camera mount for sprint 2, added laser cut files for tape runner
    [bottom_runner.DXF, bottom_runner.SLDPRT, camera_motherboard_mount.SLDPRT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]
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2023-11-09 x axis suff, fix sprocket
    [3764N107_High-Strength Gt Timing Belt Pulley.SLDPRT, 3764N113_High-Strength Gt Timing Belt Pulley.SLDPRT, SG90 - Micro Servo 9g - Tower Pro.1.SLDPRT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]
2023-11-09 Finished rev 1 of tape tension system
    [Arm.SLDPRT, Arm_roller.DXF, Arm_spring.DXF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]
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2023-11-10 Added cable management to box side panel, created drawing for tape clamp
    [3764N107_High-Strength Gt Timing Belt Pulley.SLDPRT, 3764N113_High-Strength Gt Timing Belt Pulley.SLDPRT, Roller_3dp.SLDPRT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]
2023-11-10 beginning of baseplate cad
    [90592A090_Steel Hex Nut.SLDPRT, table.SLDPRT, wheel_hinge_2x.SLDPRT]
2023-11-11 added files from local folder
    [91292A199_18-8 Stainless Steel Socket Head Screw.SLDPRT, spool_assembly.SLDASM, spool_sides_v2.DWG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]
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2023-11-12 fix main assembly errors hopefully
    [3764N107_High-Strength Gt Timing Belt Pulley.SLDPRT, 3764N113_High-Strength Gt Timing Belt Pulley.SLDPRT, SG90 - Micro Servo 9g - Tower Pro.SLDASM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]
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2023-11-16 fix write head part
    [3764N107_High-Strength Gt Timing Belt Pulley.SLDPRT, 3764N113_High-Strength Gt Timing Belt Pulley.SLDPRT, write_rev_3.SLDASM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]
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2023-11-18 Added first draft of camera shroud, modified tape roller, and added MK3 directory
    [##Servo_MG_996R.SLDPRT, 3764N107_High-Strength Gt Timing Belt Pulley.SLDPRT, 3764N113_High-Strength Gt Timing Belt Pulley.SLDPRT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]
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2023-11-27 further minor changes spring tension
    hole sizes got confused, rollers want to take an M5 not an M4
    [Arm.SLDPRT, Arm_roller.DXF, Tape_tesnion.SLDASM]
2023-11-27 fix write head
    [rod_holder_rev2_servo_side.SLDPRT, rod_holder_rev2_servo_side_mk2.STL, write_rev_3.SLDASM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]
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2023-11-28 fixing github thing
    [Roller.SLDPRT, Roller_3dp.STL, Spacer_3dp.STL]
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2023-11-28 Update block diagram
    Change block diagram to show use of only one Motor Shield.
    Replace eraser solenoid with servo.
2023-11-29 fixed erase head
    fixed erase head
    [3764N107_High-Strength Gt Timing Belt Pulley.SLDPRT, 3764N113_High-Strength Gt Timing Belt Pulley.SLDPRT, SG90 - Micro Servo 9g - Tower Pro.SLDASM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]
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2023-11-30 Symbol rec (test) - working for 0 and 1
    [dataset.csv]
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2023-12-02 Adjusted hole sizing on delrin top
    The holes that are supposed to be tapped now can be and vise versa
    [box_faces.SLDPRT, box_top_delrin.DXF]
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2023-12-04 Start lcd mount, render images
    also delete unessecary files
    [box_faces.SLDPRT, eraser_motor.SLDPRT, lcd_plate.SLDPRT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]
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2023-12-04 finish lcd mount
    still need to add actual dimensions once it comes
    [3764N107_High-Strength Gt Timing Belt Pulley.SLDPRT, 3764N113_High-Strength Gt Timing Belt Pulley.SLDPRT, Rocker Safety Switch.step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]
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2023-12-05 write head rev 3
    - add a taper to better match the marker's profile (may need to reduce press fit)
    - add little bit at bottom for better support
    - reduce hole diameters
    - add pretty fillets
    [3764N107_High-Strength Gt Timing Belt Pulley.SLDPRT, 3764N113_High-Strength Gt Timing Belt Pulley.SLDPRT, write_rev_3.SLDASM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]
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2023-12-08 Add goToCamera function and fix goHome
    [TM_Motor_Movement.cpp, motor_functions.ino]
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2023-12-08 Fix motor spin direction in eraseAll
    [TM_Motor_Movement.cpp]
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
